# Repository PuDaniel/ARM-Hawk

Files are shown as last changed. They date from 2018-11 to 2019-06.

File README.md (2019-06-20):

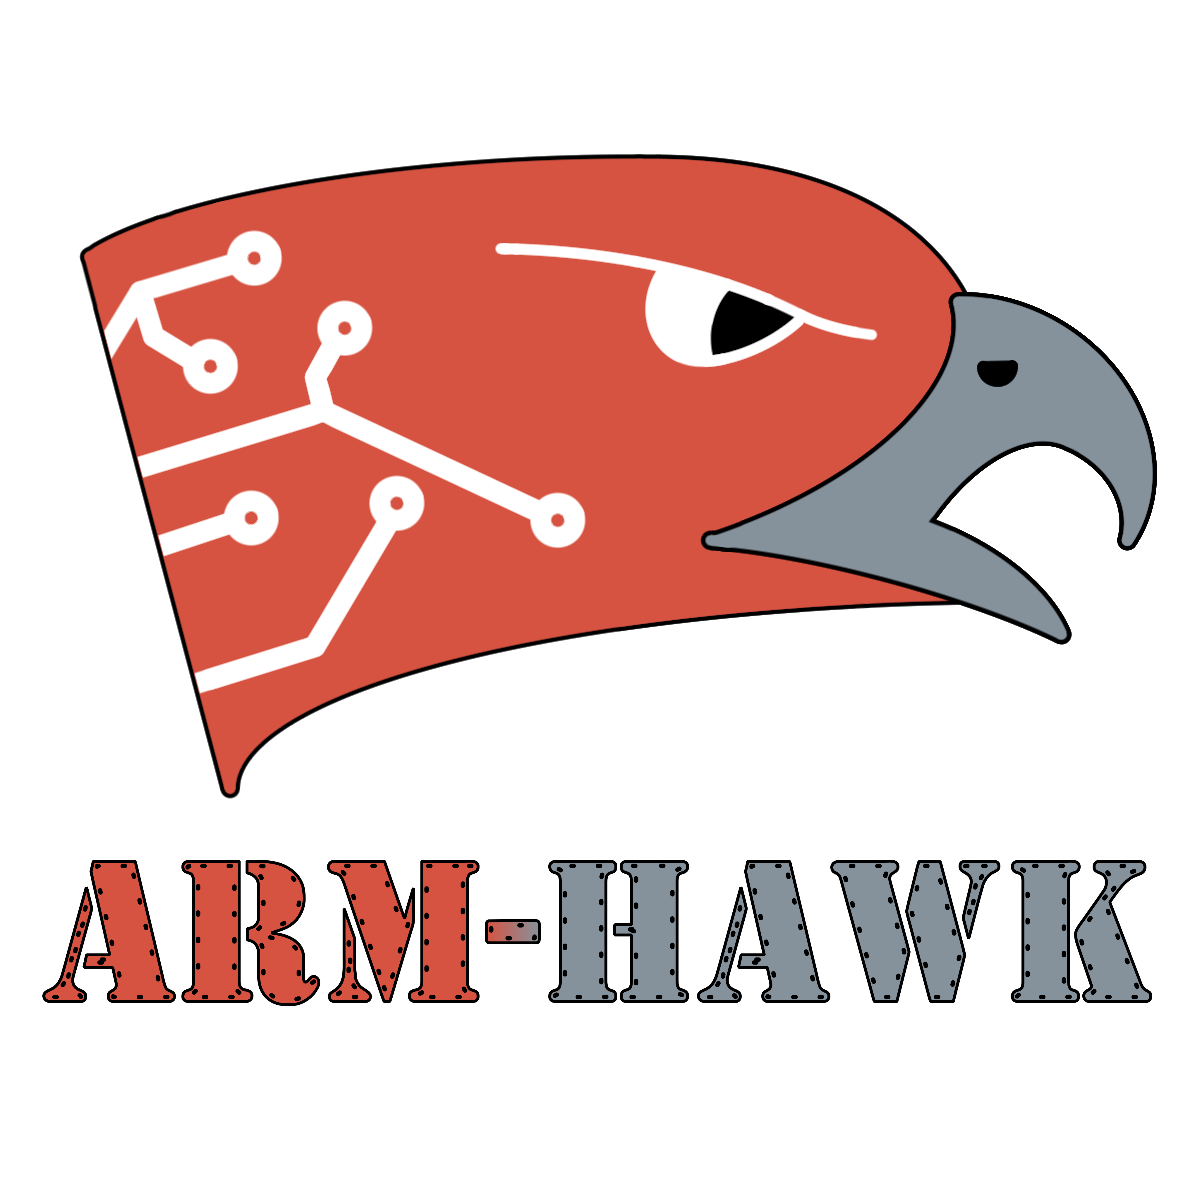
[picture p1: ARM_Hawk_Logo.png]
ARM-Hawk Logo


The ARM-Hawk project consists of a custom designed radio controlled airplane equipped with a scratch built flight computer running custom software. The goal of the project is to develop a system to greatly enhance the flight characteristics of the airplane, as well as to protect its flight envelope.
This repository includes the following parts of the project:

- [ARM_Hawk.pdf](ARM_Hawk.pdf) This file contains a complete description of the project, including the derivation of a flight model and simulation framework, sensor calibration and state estimation algorithms, and the control laws for lateral stability augmentation and stall protection
- [Air_Data_Sensor_Unit](Air_Data_Sensor_Unit) This directory contains information for building and calibrating the custom developed Air Data Probe
- [Airframe](Airframe) This directory contains some information about the airplane used
- [Electronics](Electronics) This directory contains plans for some electronic circuits (RPM sensor, servo switch)
- [Flight_Computer](Flight_Computer) This directory contains the C++ code for the flight software
- [IMU](IMU) This directory contains information for building and calibrating the custom developed Inertial Measurement Unit, as well as a model of the state estimation algorithm

Visit the project's YouTube channel to see some videos of the system in action:
[https://m.youtube.com/channel/UCTHfZXQw1zonnjaXaEWrNzA](https://m.youtube.com/channel/UCTHfZXQw1zonnjaXaEWrNzA)

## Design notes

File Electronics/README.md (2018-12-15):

# Electronics

This directory contains all custom developed circuits used in the ARM-Hawk project.

### Brushless RPM sensor

This sensor is connected to two of the three BLDC motor's phases. It outputs a square wave with a frequency equal to that of the electric field's frequency.

- [Brushless_RPM_sensor/CAM](Brushless_RPM_sensor/CAM) contains g-code files for milling the PCB
- [Brushless_RPM_sensor/KiCad](Brushless_RPM_sensor/KiCad) contains the KiCAD project, as well as the PCB's gerber files

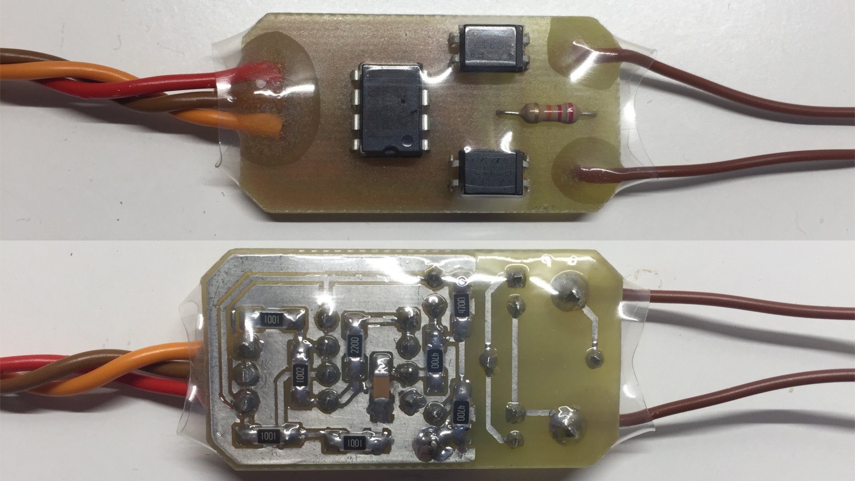
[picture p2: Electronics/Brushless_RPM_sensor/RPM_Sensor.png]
Brushless RPM sensor


### Servoswitch

The servoswitch multiplexes the servo PWM signals coming either form the flight computer or the RC receiver. A PWM channel from the RC receiver can switch all four channel outputs between these two input sources. An ATtiny13 microcontroller executes the task of switching. Many failsafe features are included in the design.

- [Servoswitch/Code](Servoswitch/Code) contains the C program for the microcontroller
- [Servoswitch/KiCad](Servoswitch/KiCad) contains the KiCAD project (only schematic)

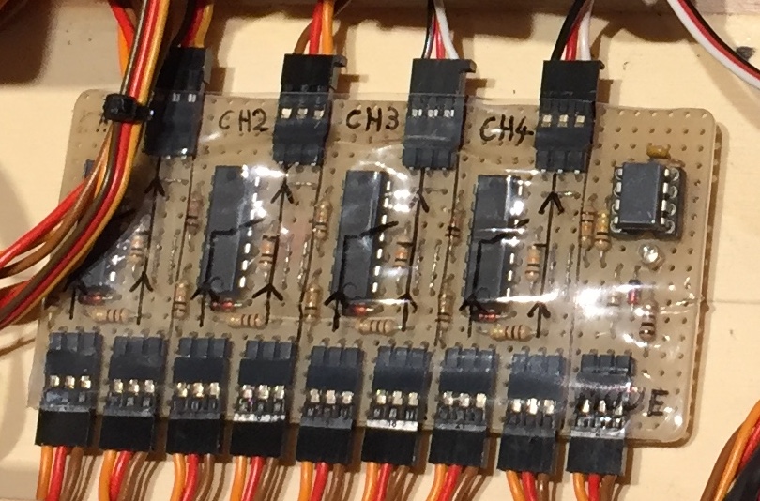
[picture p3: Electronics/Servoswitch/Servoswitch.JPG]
Servoswitch


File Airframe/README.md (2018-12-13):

# Airframe

This directory contains a general plan of the used airplane (custom built) and a *Blender* file of the assembly.

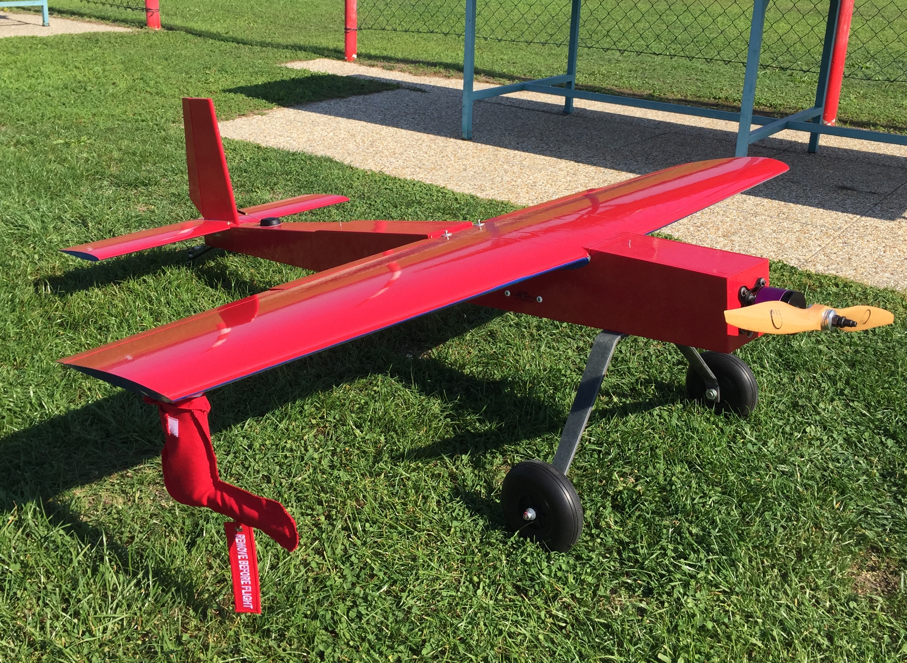
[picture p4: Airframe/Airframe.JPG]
Airframe


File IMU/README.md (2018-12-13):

# IMU

This directory contains all plans to build and calibrate the ARM-Hawk custom designed IMU. It consits of an *NXP FXAS21002* gyroscope and an *NXP FXOS8700* accelerometer/magnetometer. A CNC-machined baseplate provides an exact reference for calibration and mounting in the plane. A 3D-printed case protects the sensor ICs form high-current cables (magnetic fields).

- [Calibration_accelerometer](Calibration_accelerometer) contains a Matlab script to calibrate the accelerometer (a sample dataset and result is also included)
- [Calibration_gyro](Calibration_gyro) contains a Matlab script to calibrate the gyroscope (a sample dataset and result is also included)
- [Calibration_magnetometer](Calibration_magnetometer) contains two Matlab scripts to calibrate the magnetometer for the static case and the dynamic case with the motor running (a sample dataset and result is also included)
- [CAM](CAM) contains the g-code files needed for milling the baseplate (floor), the spacer and the interface PCB, as well as an STL file for 3D-printing the case
- [Jig](Jig) contains a g-code file to mill an alignment jig needed for calibration from an 1.5mm glassfibre plate
- [PCB](PCB) contains the KiCad project of the interface circuit and the PCB's gerber files
- [Simulation](Simulation) contains a *Simulink* model of the state estimation algorithm, which is performed from the flight computer in real time (a sample dataset recorded during a test flight is included)

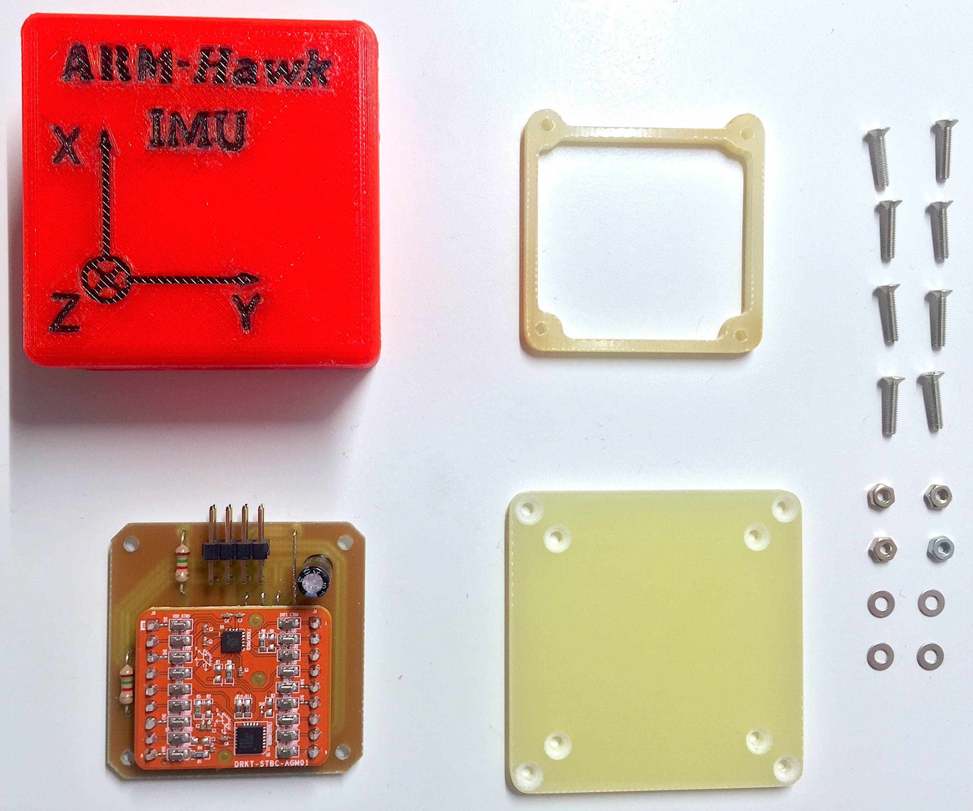
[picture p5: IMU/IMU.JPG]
IMU


CAD drawing with dimensions and rendering of the case:

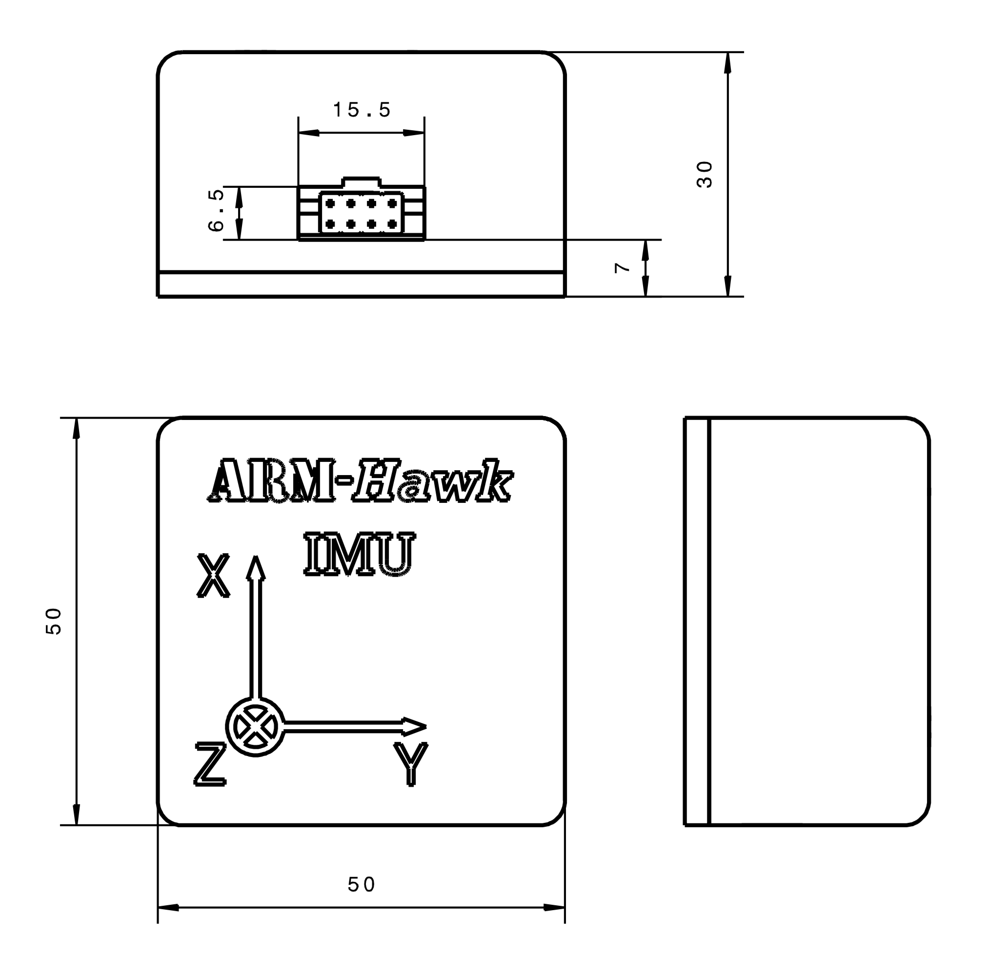
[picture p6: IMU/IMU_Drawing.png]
IMU Drawing


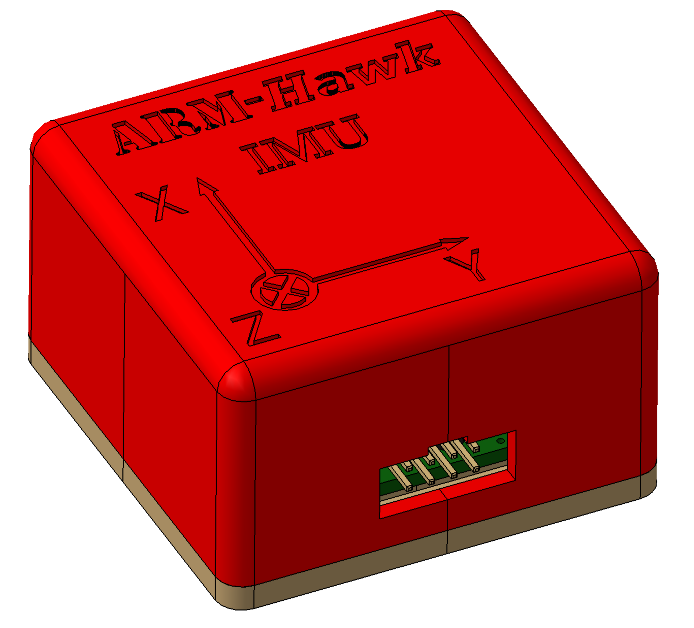
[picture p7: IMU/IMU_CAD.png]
IMU CAD


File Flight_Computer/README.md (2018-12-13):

# Flight Computer

This directory contains the flight computer's C++ software. The project has been created with *System Workbench for STM32 by AC6* ([http://www.openstm32.org](http://www.openstm32.org)).

The used hardware is an STM32F767ZI on a Nucleo development board (from ST), powered from a simple power supply providing 5V and 3.3V. Additionally, a *Sparkfun Venus638 GPS breakout* is used. All this is located in the rear equipment bay of the plane:

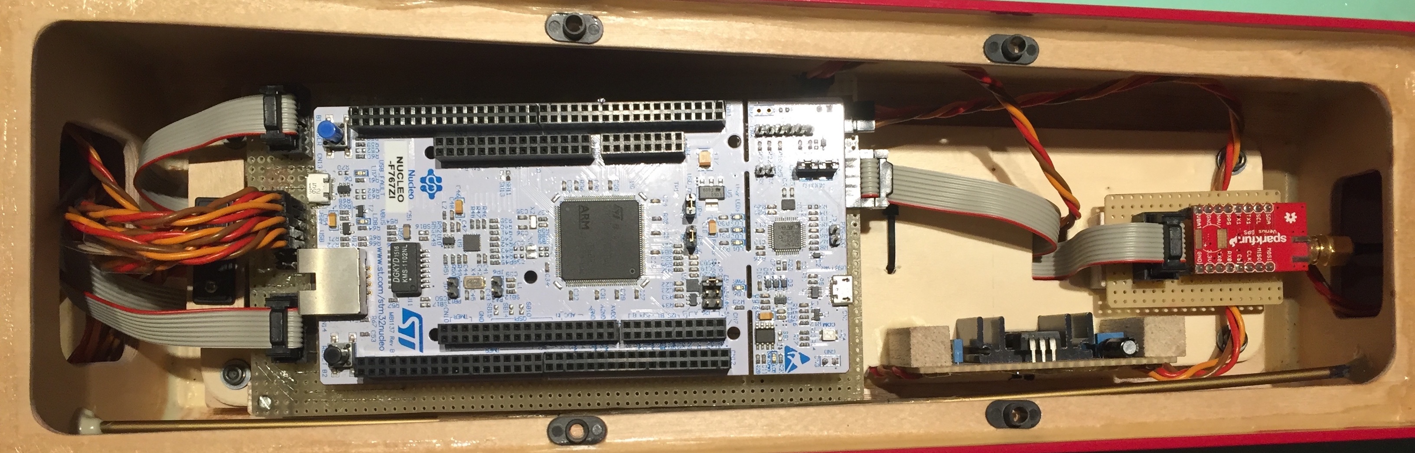
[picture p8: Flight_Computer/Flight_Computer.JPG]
Flight Computer


The Nucleo board is connected to all sensors and the datalog via a prototype interface PCB:

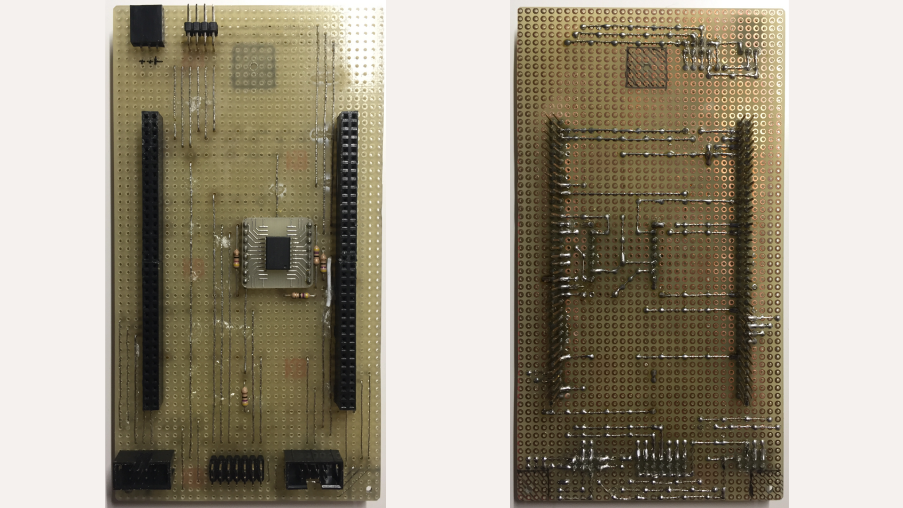
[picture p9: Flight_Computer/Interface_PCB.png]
Interface PCB


The forward (underwing) equpiment area holds the RC equipment, as well as the [Servoswitch](/Electronics/Servoswitch) and the [IMU](/IMU):

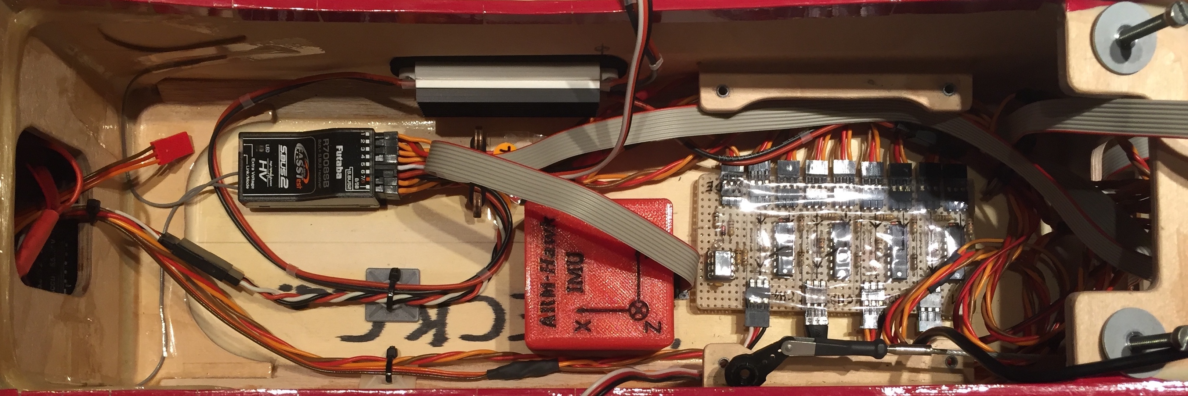
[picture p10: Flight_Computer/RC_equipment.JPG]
RC equipment


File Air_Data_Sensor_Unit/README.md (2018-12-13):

# Air Data Sensor Unit

This directory contains all plans to build the mechanical and electronical assembly of the Air Data Sensor Unit, as well as supporting files for obtaining calibrated measurements.

- [CAM](CAM) contains the g-code files for milling the two aluminum pieces (base and tip), the glassfibre mount, and the PCB, as well as STL files for the housing (3D-printed with PLA)
- [CFD](CFD) contains the pressure coefficient at the probe's tip computed with *ANSYS*, as well as the calibration curve for the static pressure port
- [Matlab](Matlab) contains three scripts for calculating the realtions between differential pressures and the flow parameters (airspeed, alpha, beta), as well as a set of precomputed characteristics:
  - *alpha_beta_algorithm.m* Computes alpha, beta and airspeed from the three measured differential pressures iteratively
  - *characterisitic.m* Computes and plots characteristic curves of alpha and beta for fixed total pressures
  - *lookup_table.m* Computes a lookup table to be used in real time from the flight computer (result of script is found in [AirDataComputer_data.cpp](/Flight_Computer/Main/sensors/AirDataComputer_data.cpp))
- [PCB](PCB) contains the KiCad project of the sensor circuit, along with the gerber files of the PCB

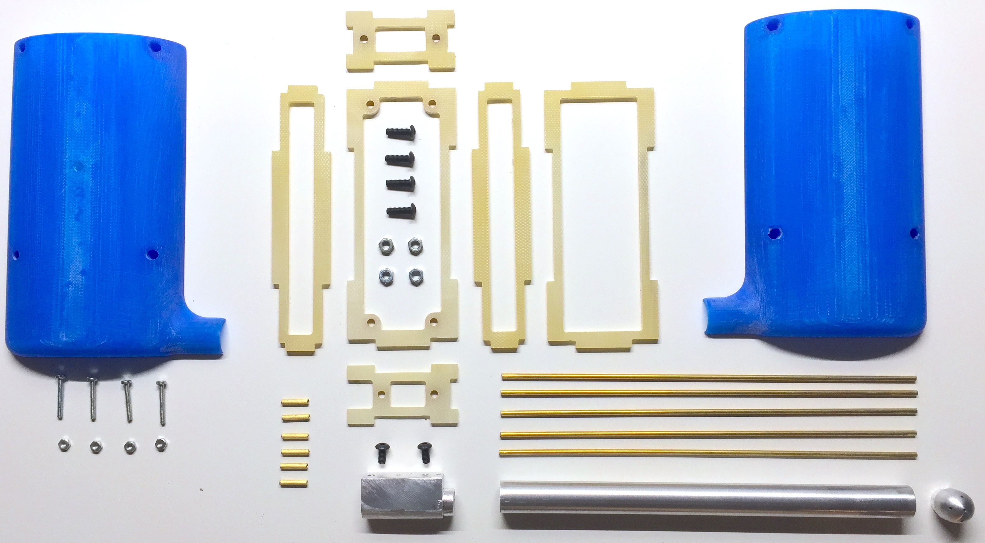
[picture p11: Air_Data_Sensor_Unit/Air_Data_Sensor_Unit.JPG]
Air Data Sensor Unit


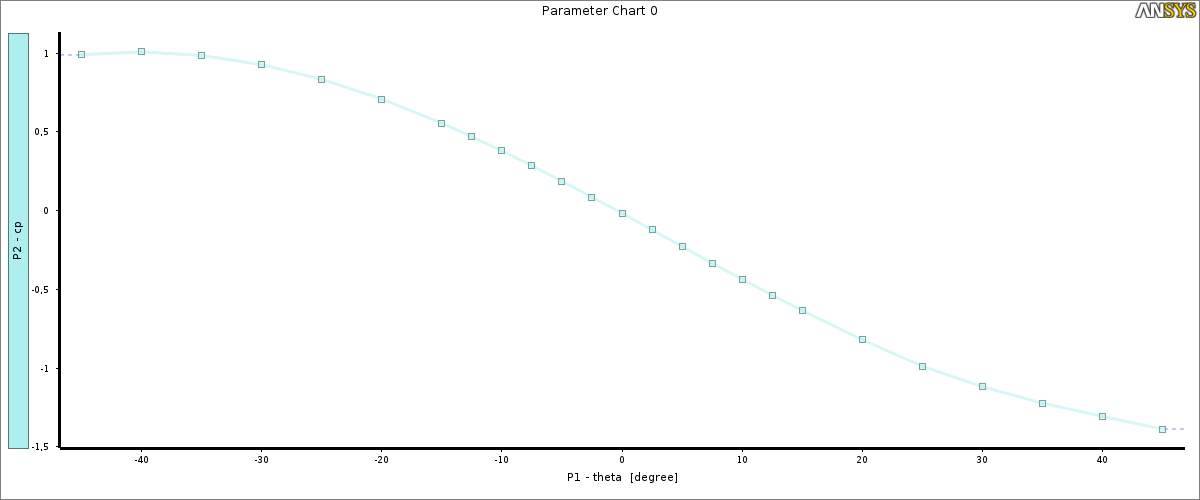
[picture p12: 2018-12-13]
Air_Data_Sensor_Unit/CFD/cp_over_theta.png

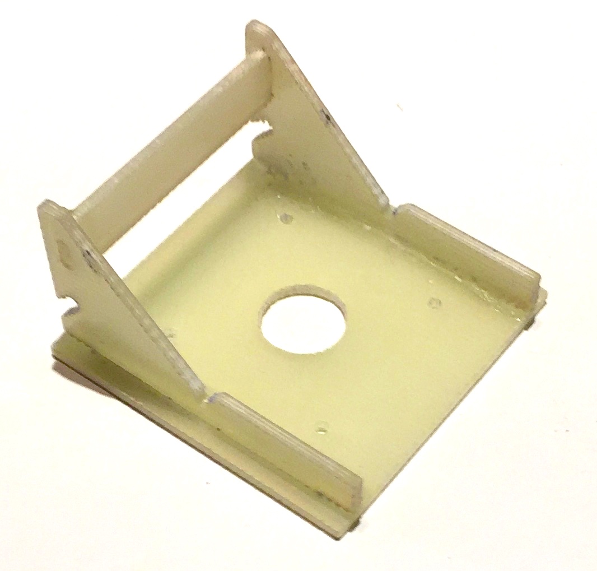
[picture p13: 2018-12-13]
IMU/Jig/Jig.JPG

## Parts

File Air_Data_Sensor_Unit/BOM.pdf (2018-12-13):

### Air Data Sensor Unit PCB Components

Quantity | Name | Package
1 | 2x4 Pin Header 2.54mm Pitch | SMD
5 | Resistor 10k | 1206
3 | Resistor 1k | 1206
3 | Capacitor 100n | 1206
3 | NPN Transistor MMBT2222 | SOT-23
1 | SMI Pressure SensorSM9541-020C-D-C-3-S | SOIC-16W
2 | SMI Pressure Sensor SM9541-010C-D-C-3-S | SOIC-16W
1 | Sparkfun SEN-09694 BMP085 Pressure Sensor | Breakout Board

### Air Data Sensor Unit Parts

Quantity | Name | Material
1 | Sensor PCB | -
1 | Probe tip | Aluminum
1 | Probe base | Aluminum
1 | Probe tube ø10x1x150 | Aluminium
5 | Pressure tube ø0.5x0.25x150 | Brass
6 | Pressure fitting (use short sections of ø0.5x0.25 tube) | Brass
1 | Robart airline tubing (1/8’’ OD, 1/16’’ ID) | Tubing
6 | CNC cut mount pieces | Glassfibre plate 3mm
1 | 3D printed housing (left and right) | PLA
4 | Socket head cap screw M3x10 | Steel
2 | Socket head cap screw M3x6 | Steel
6 | M3 hex nut | Steel
4 | Socket head cap screw M2x12 | Steel
4 | M2 hex nut | Steel

1

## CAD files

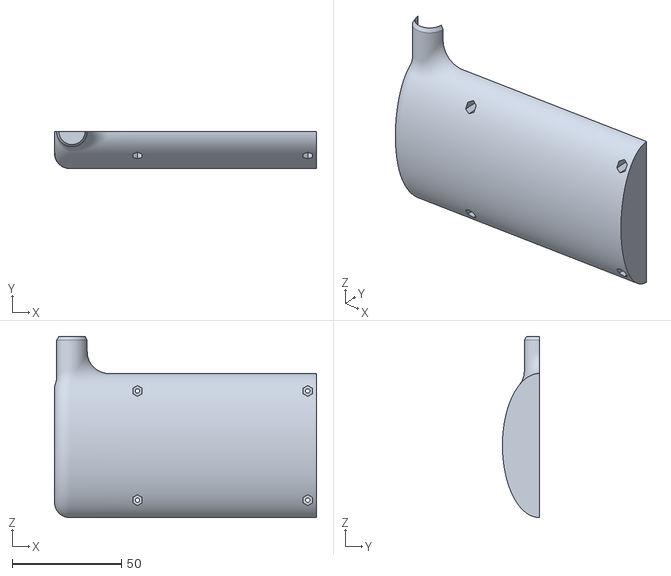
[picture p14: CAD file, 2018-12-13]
Air_Data_Sensor_Unit/CAM/Housing/housing_left.stl
120.0 x 17.0 x 83.0

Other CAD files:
Air_Data_Sensor_Unit/CAM/Housing/housing_right.stl

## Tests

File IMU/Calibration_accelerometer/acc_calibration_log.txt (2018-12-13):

 
Calibration form: f = C*(f_acc - f_0)
 
Local magnitude of gravity vector [m/s^2]=
   9.8082e+00

Calibration matrix C=
   9.8459e-01   8.0660e-04  -2.3062e-02
  -3.3592e-03   1.0027e+00   2.4024e-03
   4.9667e-03  -3.3054e-03   1.0109e+00

Acceleration bias vector f_0 [m/s^2]=
  -7.6722e-02
  -8.5341e-02
  -7.2458e-02

Error before calibration [%]=
   2.0403e+00

Error after calibration [%]=
   5.8813e-01

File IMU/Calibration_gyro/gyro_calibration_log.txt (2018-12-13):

 
Calibration form: omega_v = C*(omega_gyro - omega_0) - G*f
 
Calibration matrix C=
   1.0313e+00  -1.1339e-02  -7.2564e-03
  -7.8347e-03   9.8760e-01   7.4846e-03
   1.9856e-03   6.5120e-04   1.0242e+00

Angular rate bias vector omega_0 [rad/s]=
   6.9040e-02
  -4.8245e-02
   4.1435e-03

G-force coupling matrix G [rad*s/m]=
   1.0539e-03            0            0
            0   9.4485e-04            0
            0            0   1.2274e-03

Error before calibration [%]=
   3.2692e+00

Error after calibration [%]=
   1.0893e+00

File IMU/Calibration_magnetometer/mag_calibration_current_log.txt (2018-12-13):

 
Calibration form: B_M = S * M * B_E + B_0 + I*B_I
                  B_E = C * (B_M - B_0 - I*B_I)
 
Current dependent hard-iron offset vector B_I [T/A]=
   8.2807e-09
   1.2813e-08
  -2.3106e-08

Error before calibration [%]=
   4.0295e-01

Error before calibration [%]=
   1.6261e-01

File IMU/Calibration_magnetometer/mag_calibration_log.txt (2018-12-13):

 
Calibration form: B_M = S * M * B_E + B_0
                  B_E = (S * M)^(-1) * (B_M - B_0)
                  B_E = C * (B_M - B_0)
 
Local magnetic field vector [T]=
   2.1048e-05
   1.5839e-06
   4.3789e-05

Scale matrix S=
   9.5256e-01   2.7014e-04   1.0733e-02
   2.7014e-04   9.2349e-01   2.4467e-03
   1.0733e-02   2.4467e-03   9.3279e-01

Misalignment matrix M=
   9.9948e-01  -1.6256e-02  -2.7758e-02
   1.6420e-02   9.9985e-01   5.7045e-03
   2.7661e-02  -6.1573e-03   9.9960e-01

Calibration matrix C=
   1.0491e+00   1.7427e-02   1.7537e-02
  -1.7268e-02   1.0827e+00  -9.2422e-03
  -4.1222e-02   3.3487e-03   1.0721e+00

Hard-iron offset vector B_0 [T]=
  -1.0318e-04
  -6.9476e-05
  -7.3740e-05

Error before calibration [%]=
   4.5485e-01

Error before calibration [%]=
   2.5320e-01

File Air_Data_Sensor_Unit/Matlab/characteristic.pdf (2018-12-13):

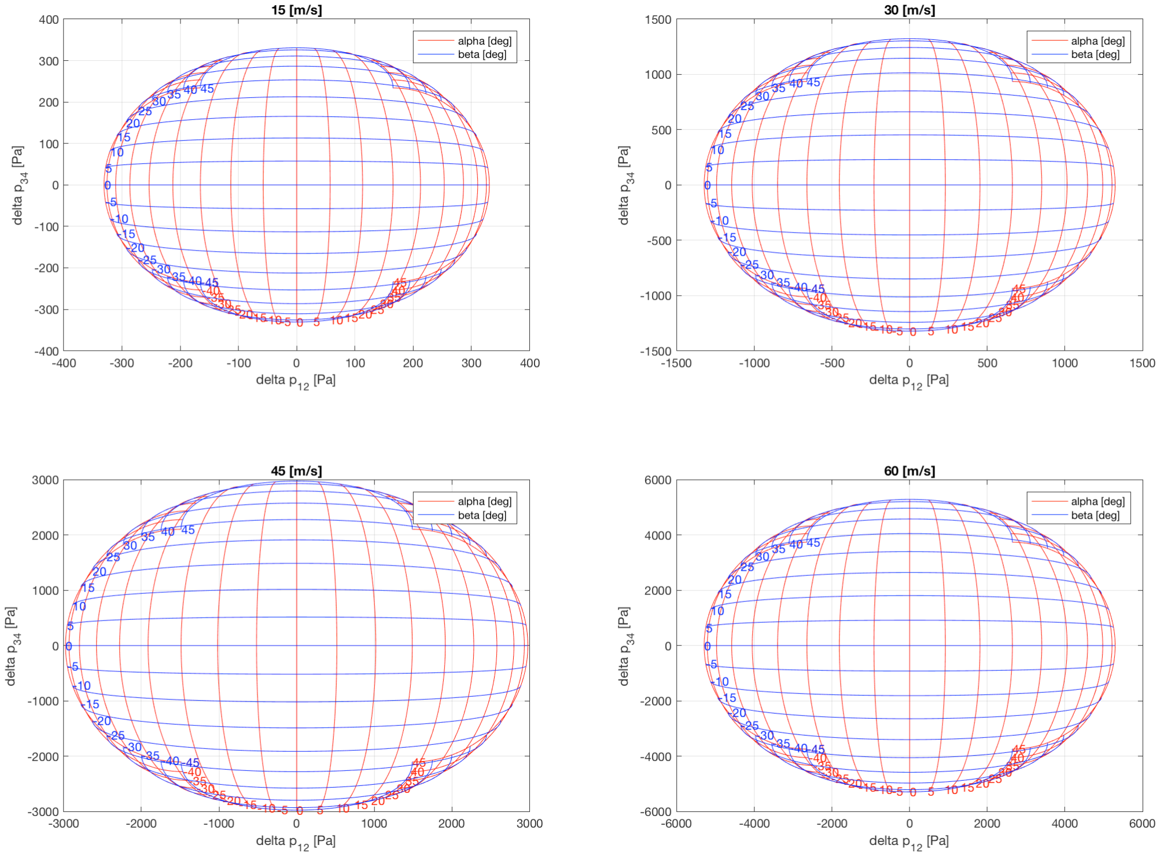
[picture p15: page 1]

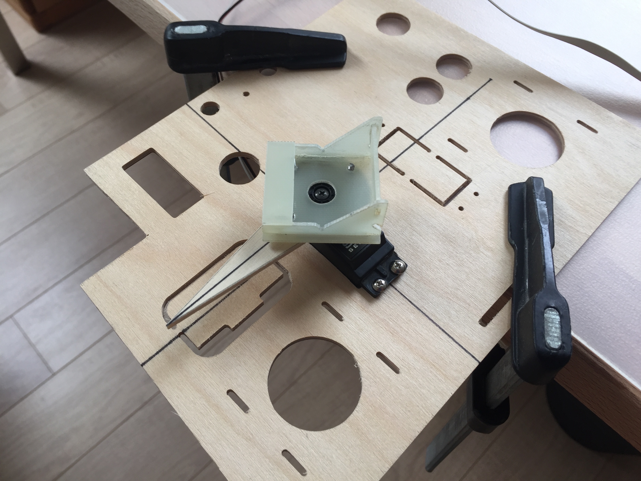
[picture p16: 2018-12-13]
IMU/Calibration_gyro/gyro_calibration_1.JPG

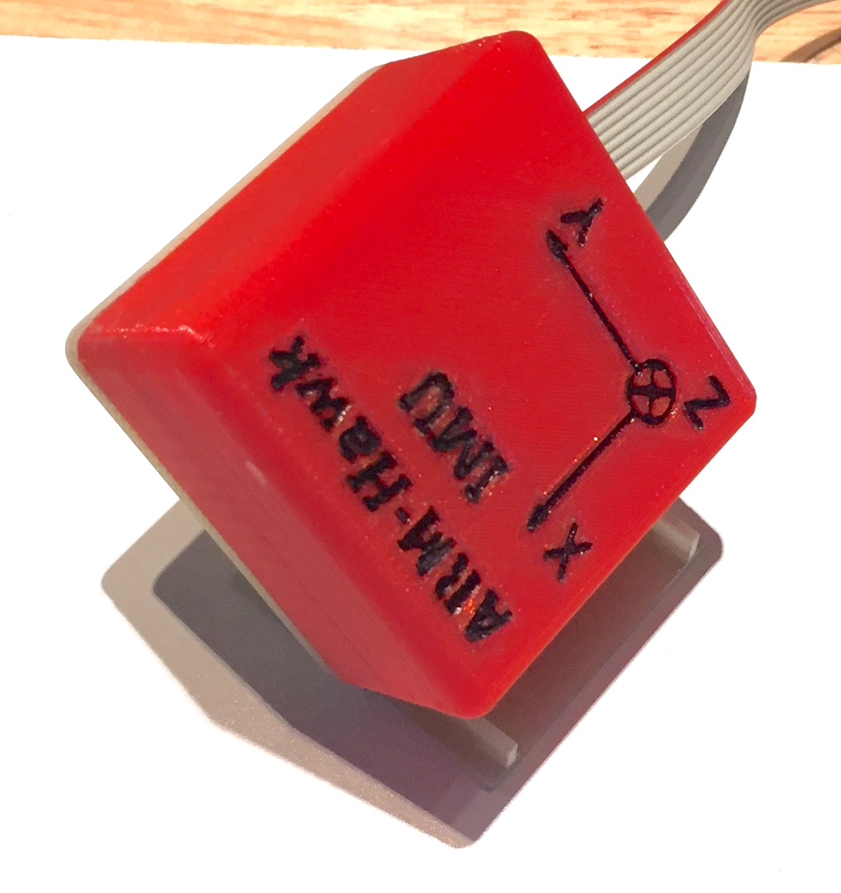
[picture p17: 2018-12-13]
IMU/Calibration_accelerometer/acc_calibration.JPG

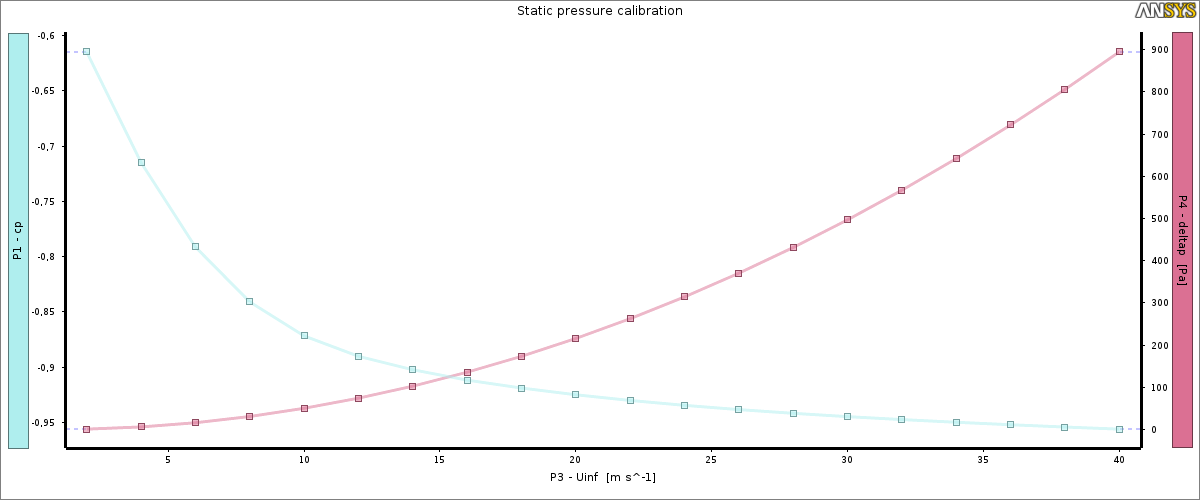
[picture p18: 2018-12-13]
Air_Data_Sensor_Unit/CFD/static_port_calibration.png

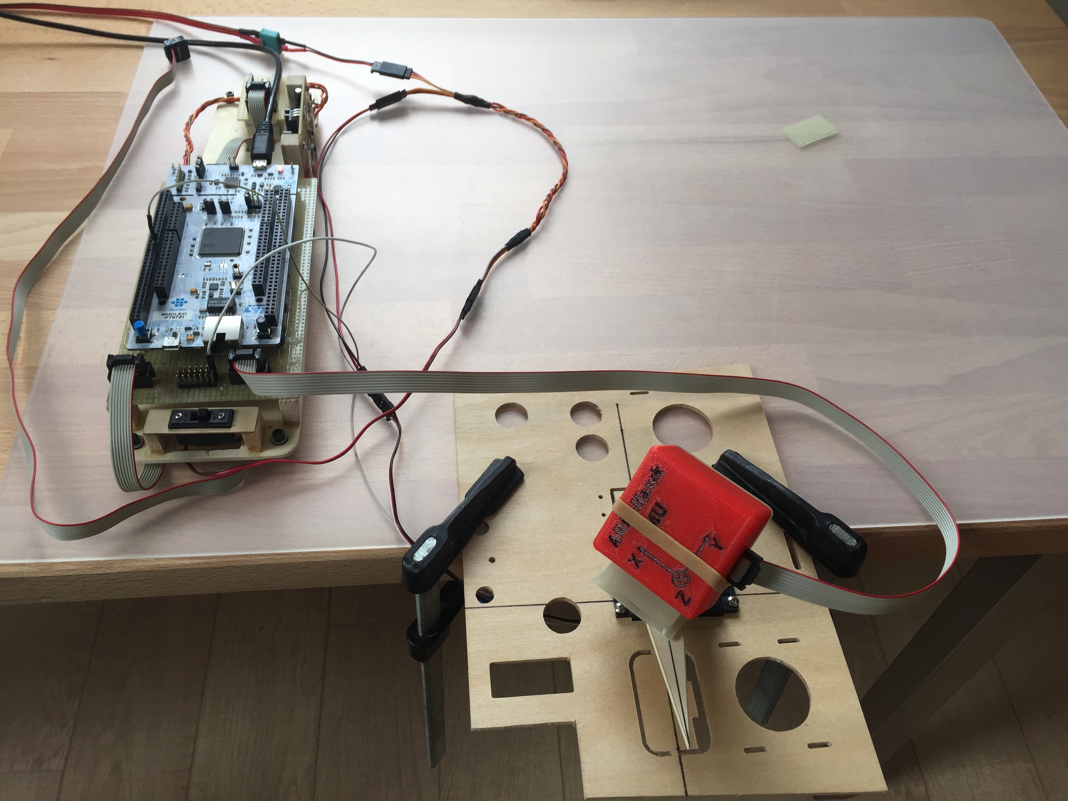
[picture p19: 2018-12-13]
IMU/Calibration_gyro/gyro_calibration_2.JPG

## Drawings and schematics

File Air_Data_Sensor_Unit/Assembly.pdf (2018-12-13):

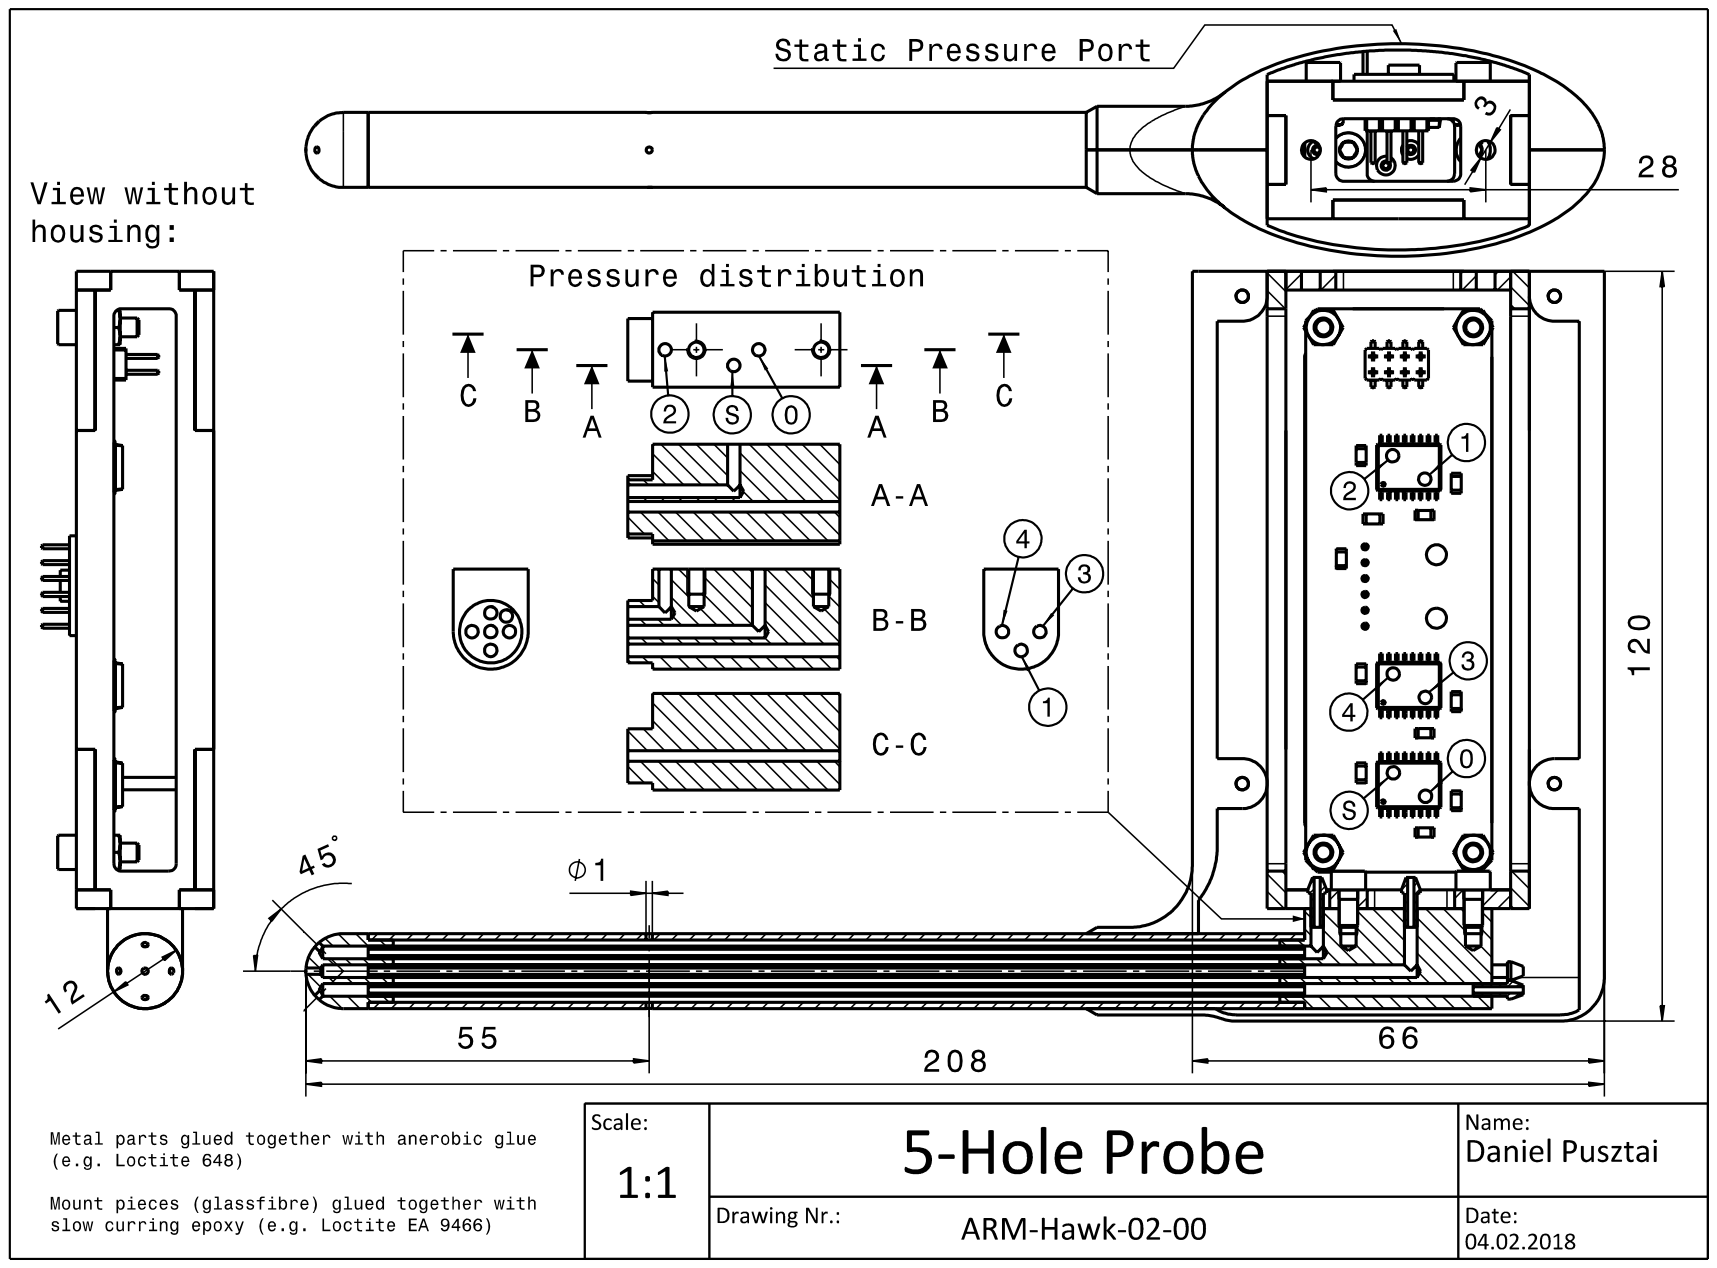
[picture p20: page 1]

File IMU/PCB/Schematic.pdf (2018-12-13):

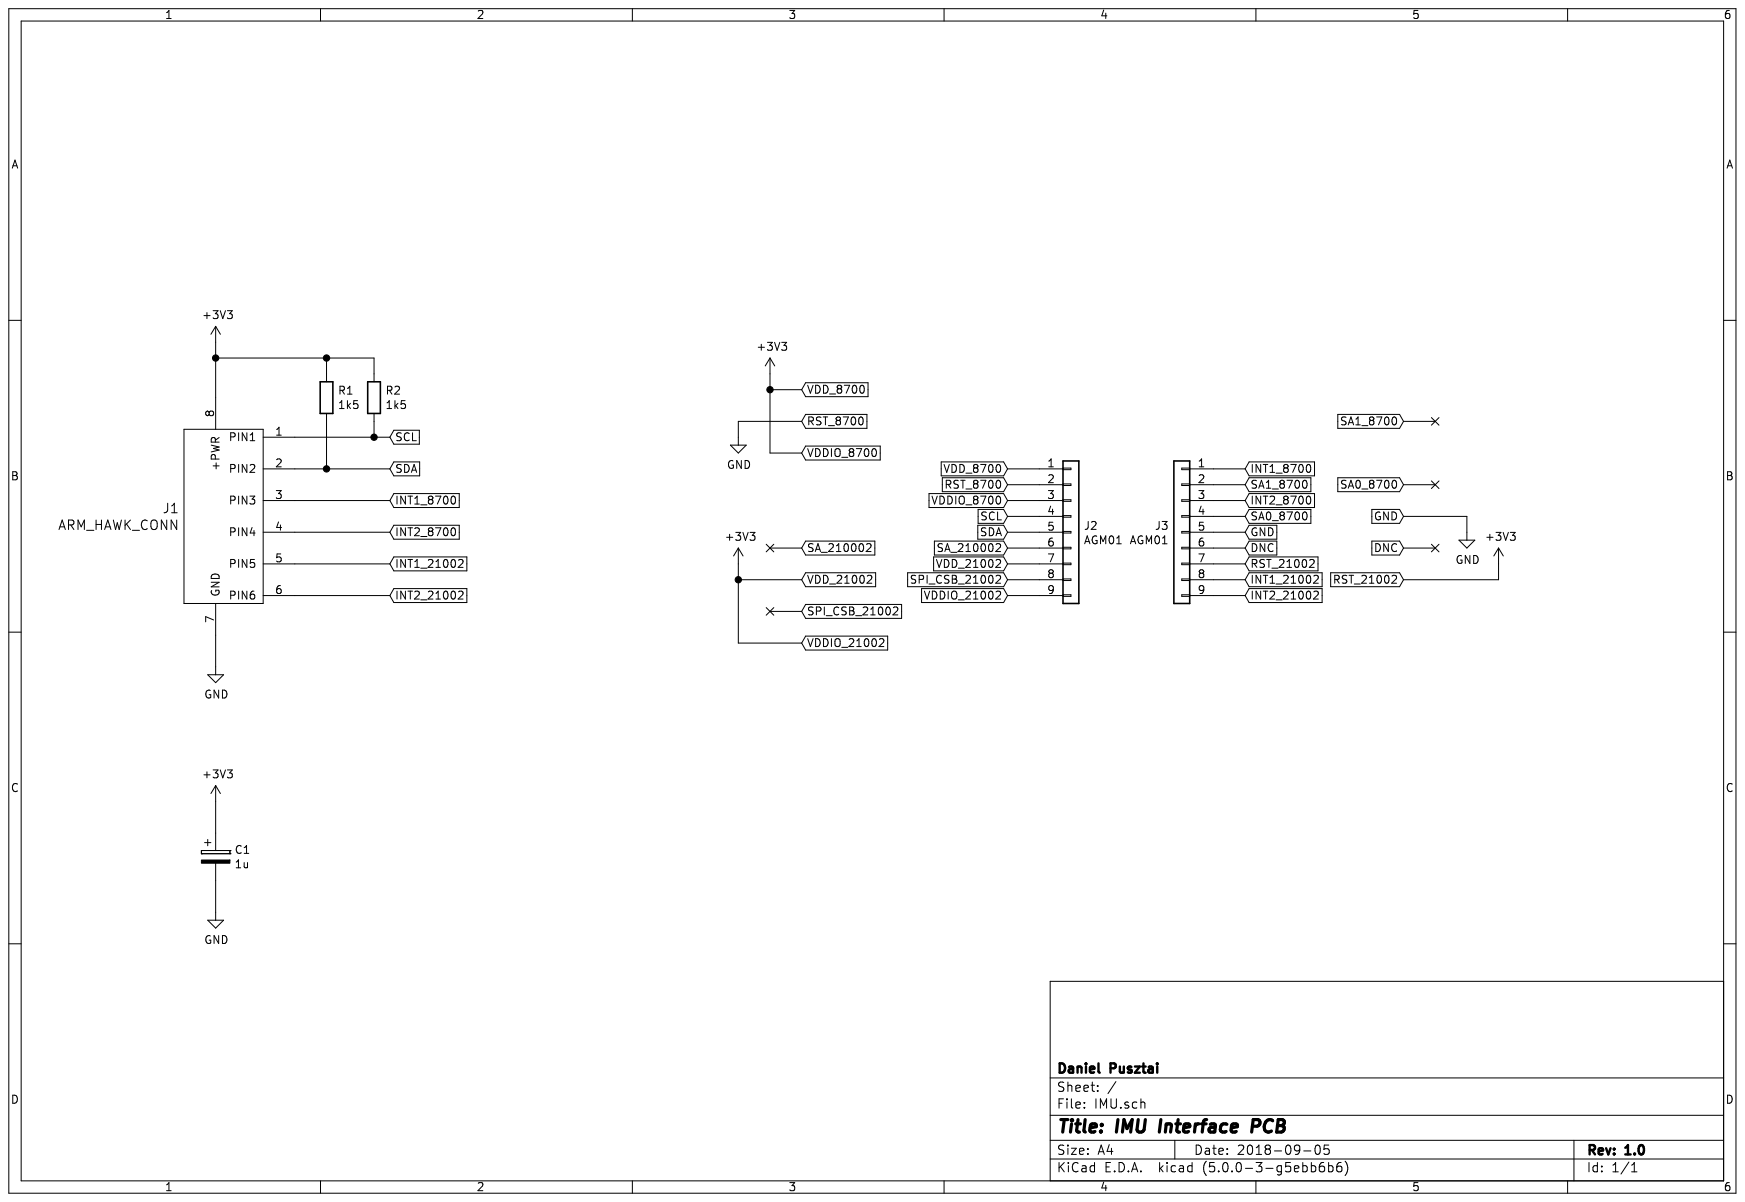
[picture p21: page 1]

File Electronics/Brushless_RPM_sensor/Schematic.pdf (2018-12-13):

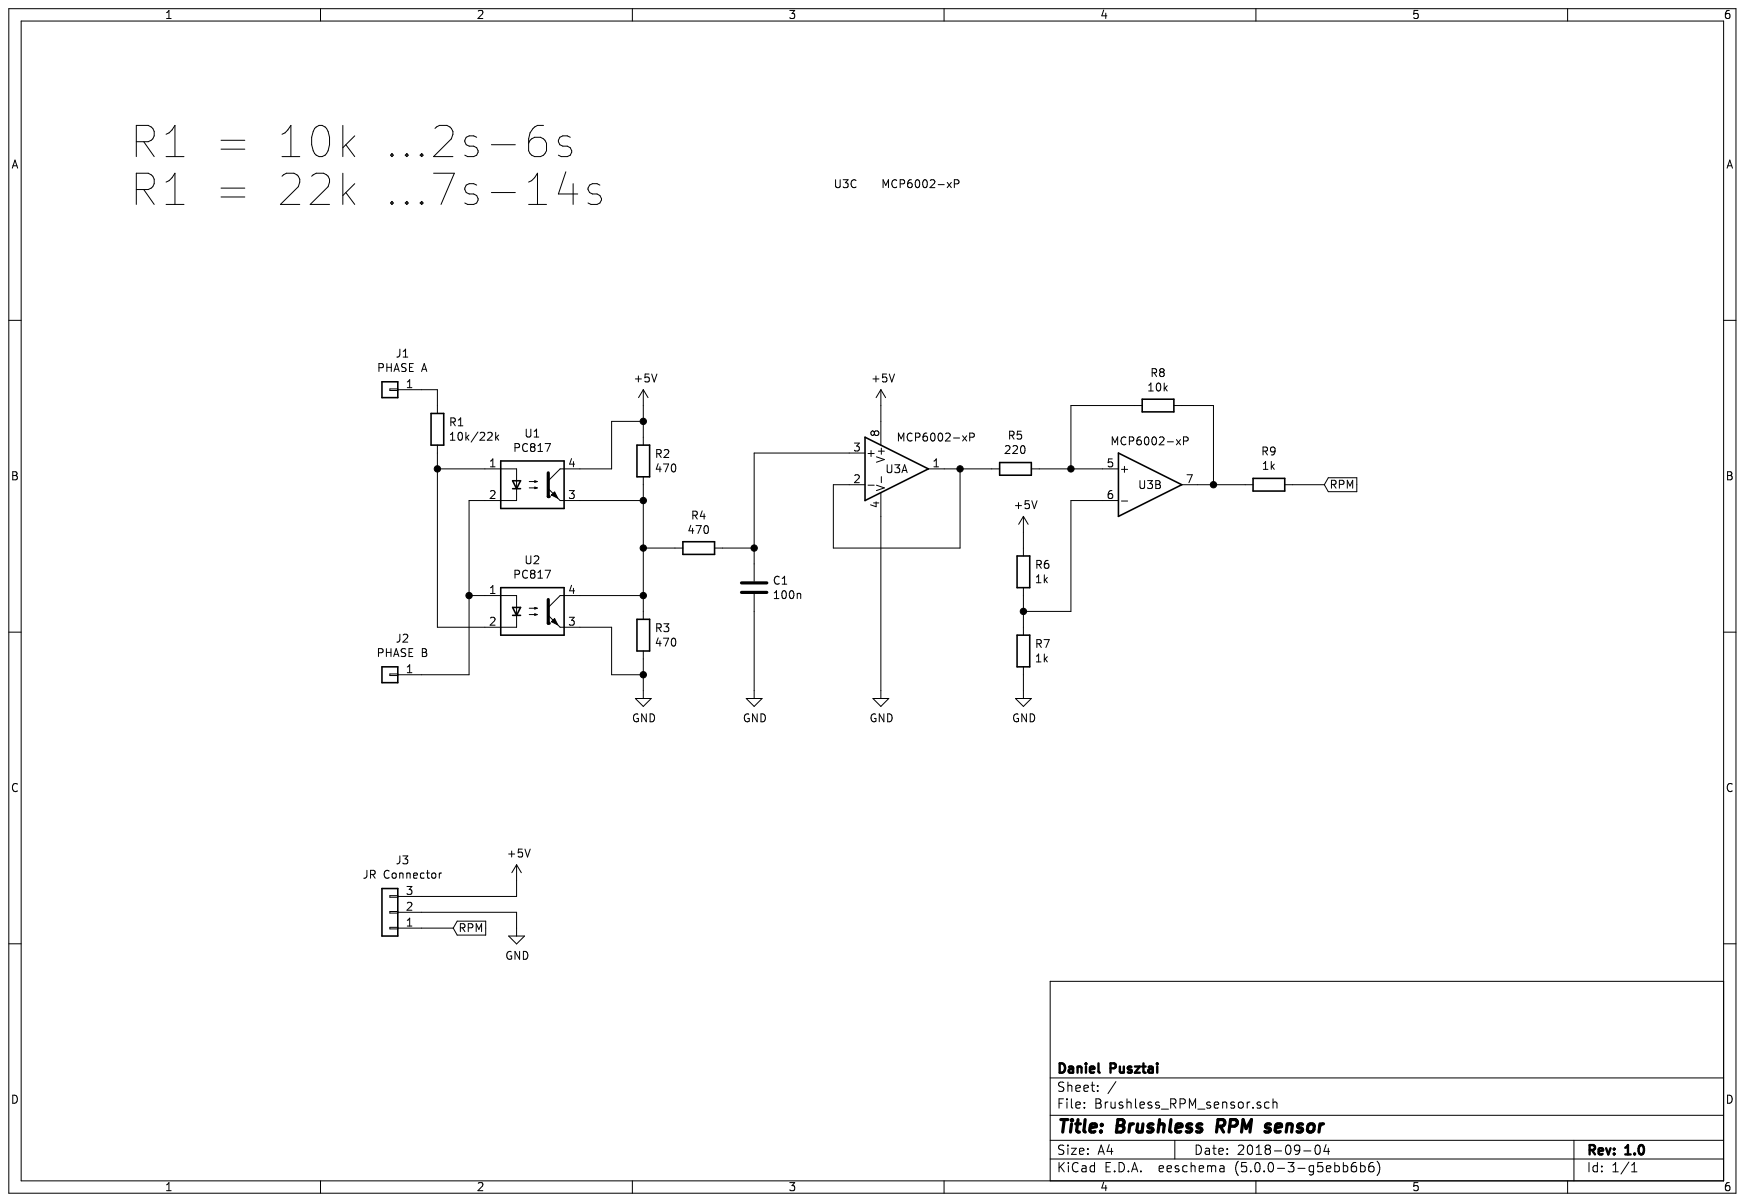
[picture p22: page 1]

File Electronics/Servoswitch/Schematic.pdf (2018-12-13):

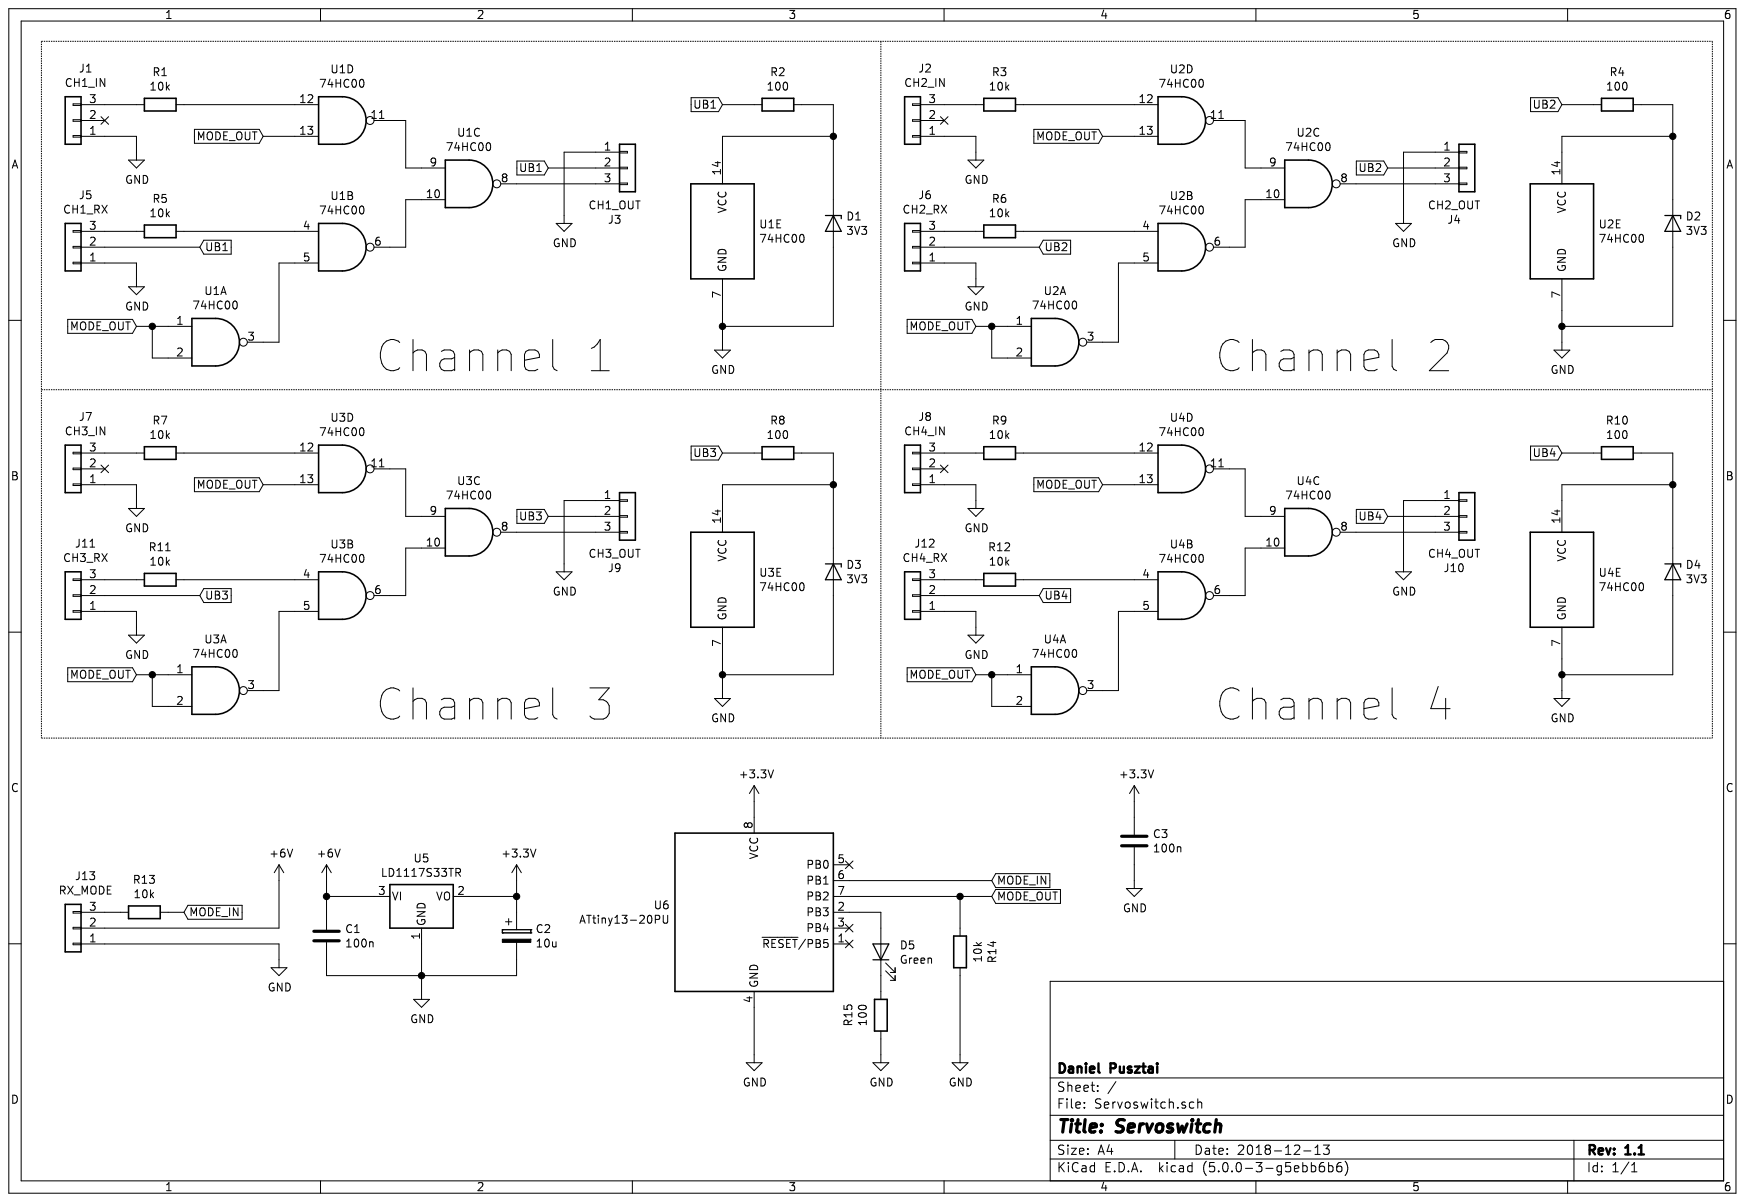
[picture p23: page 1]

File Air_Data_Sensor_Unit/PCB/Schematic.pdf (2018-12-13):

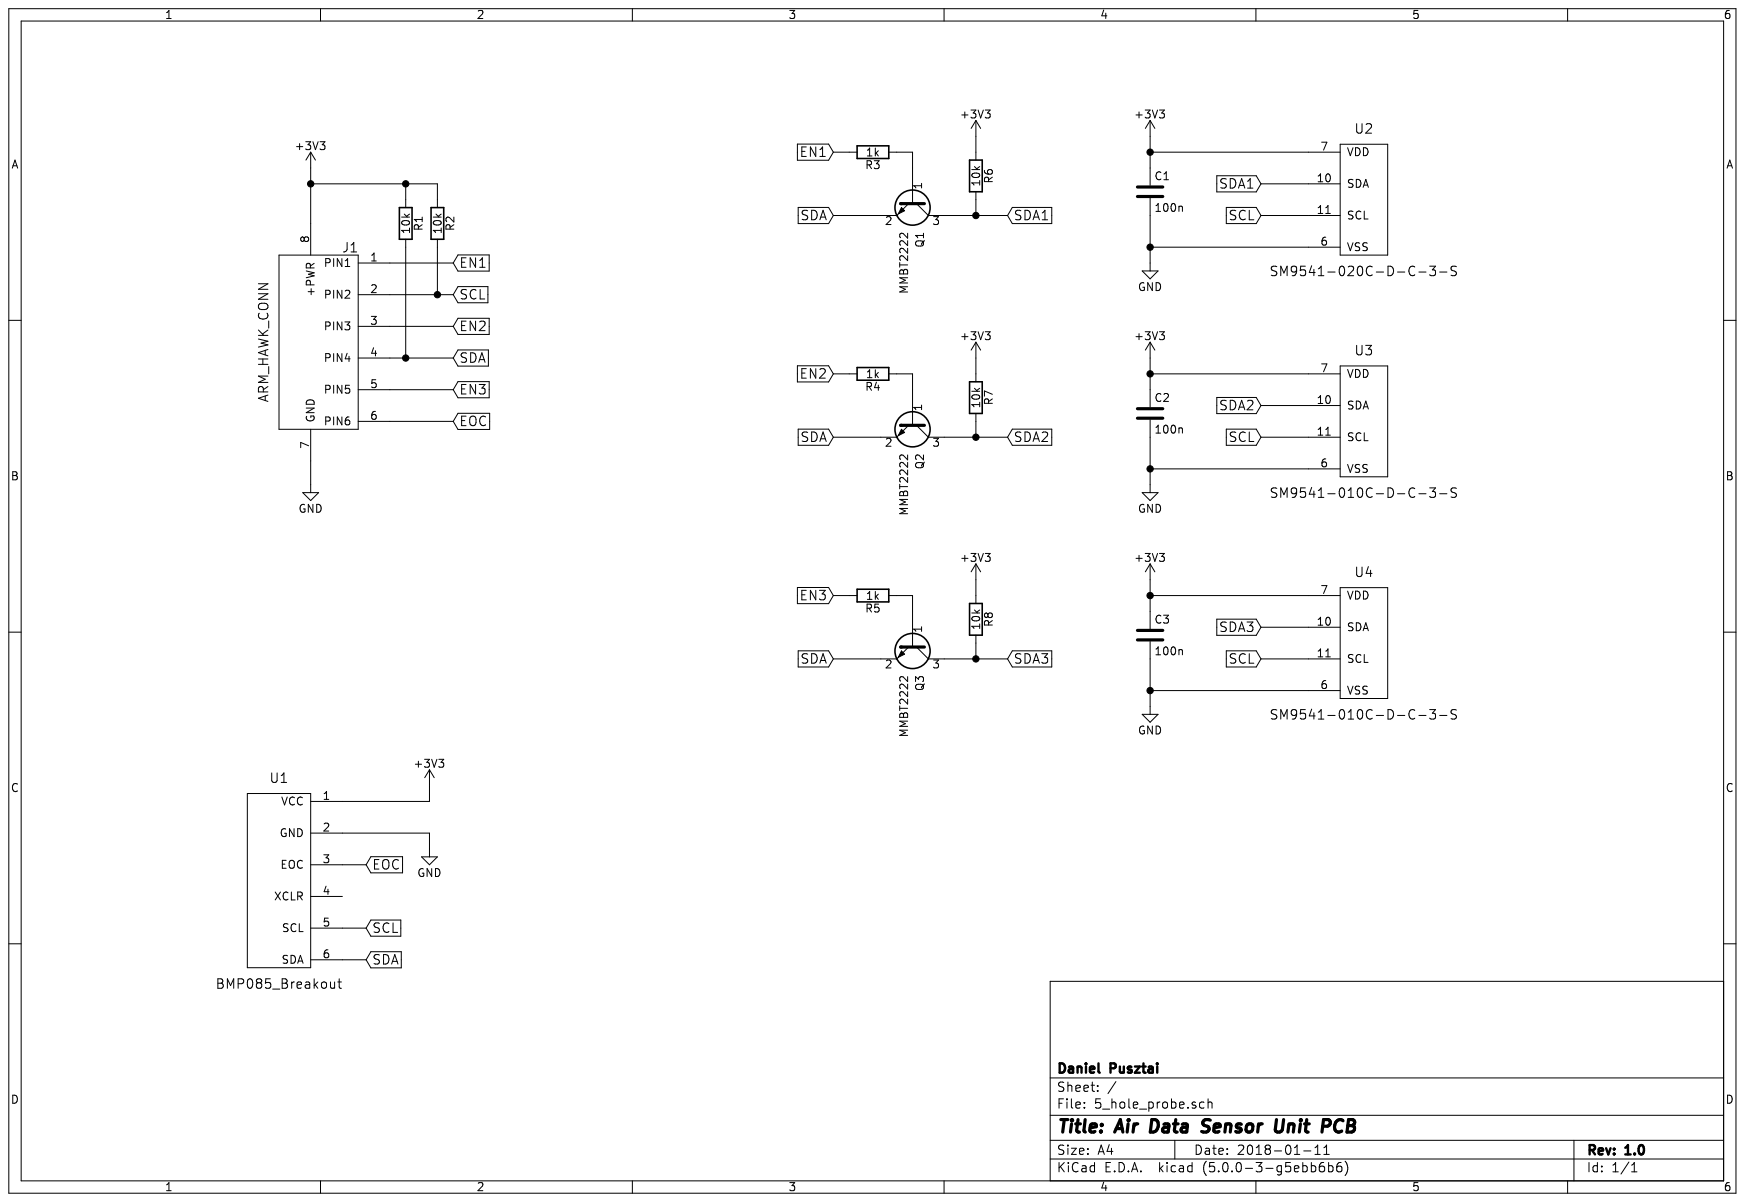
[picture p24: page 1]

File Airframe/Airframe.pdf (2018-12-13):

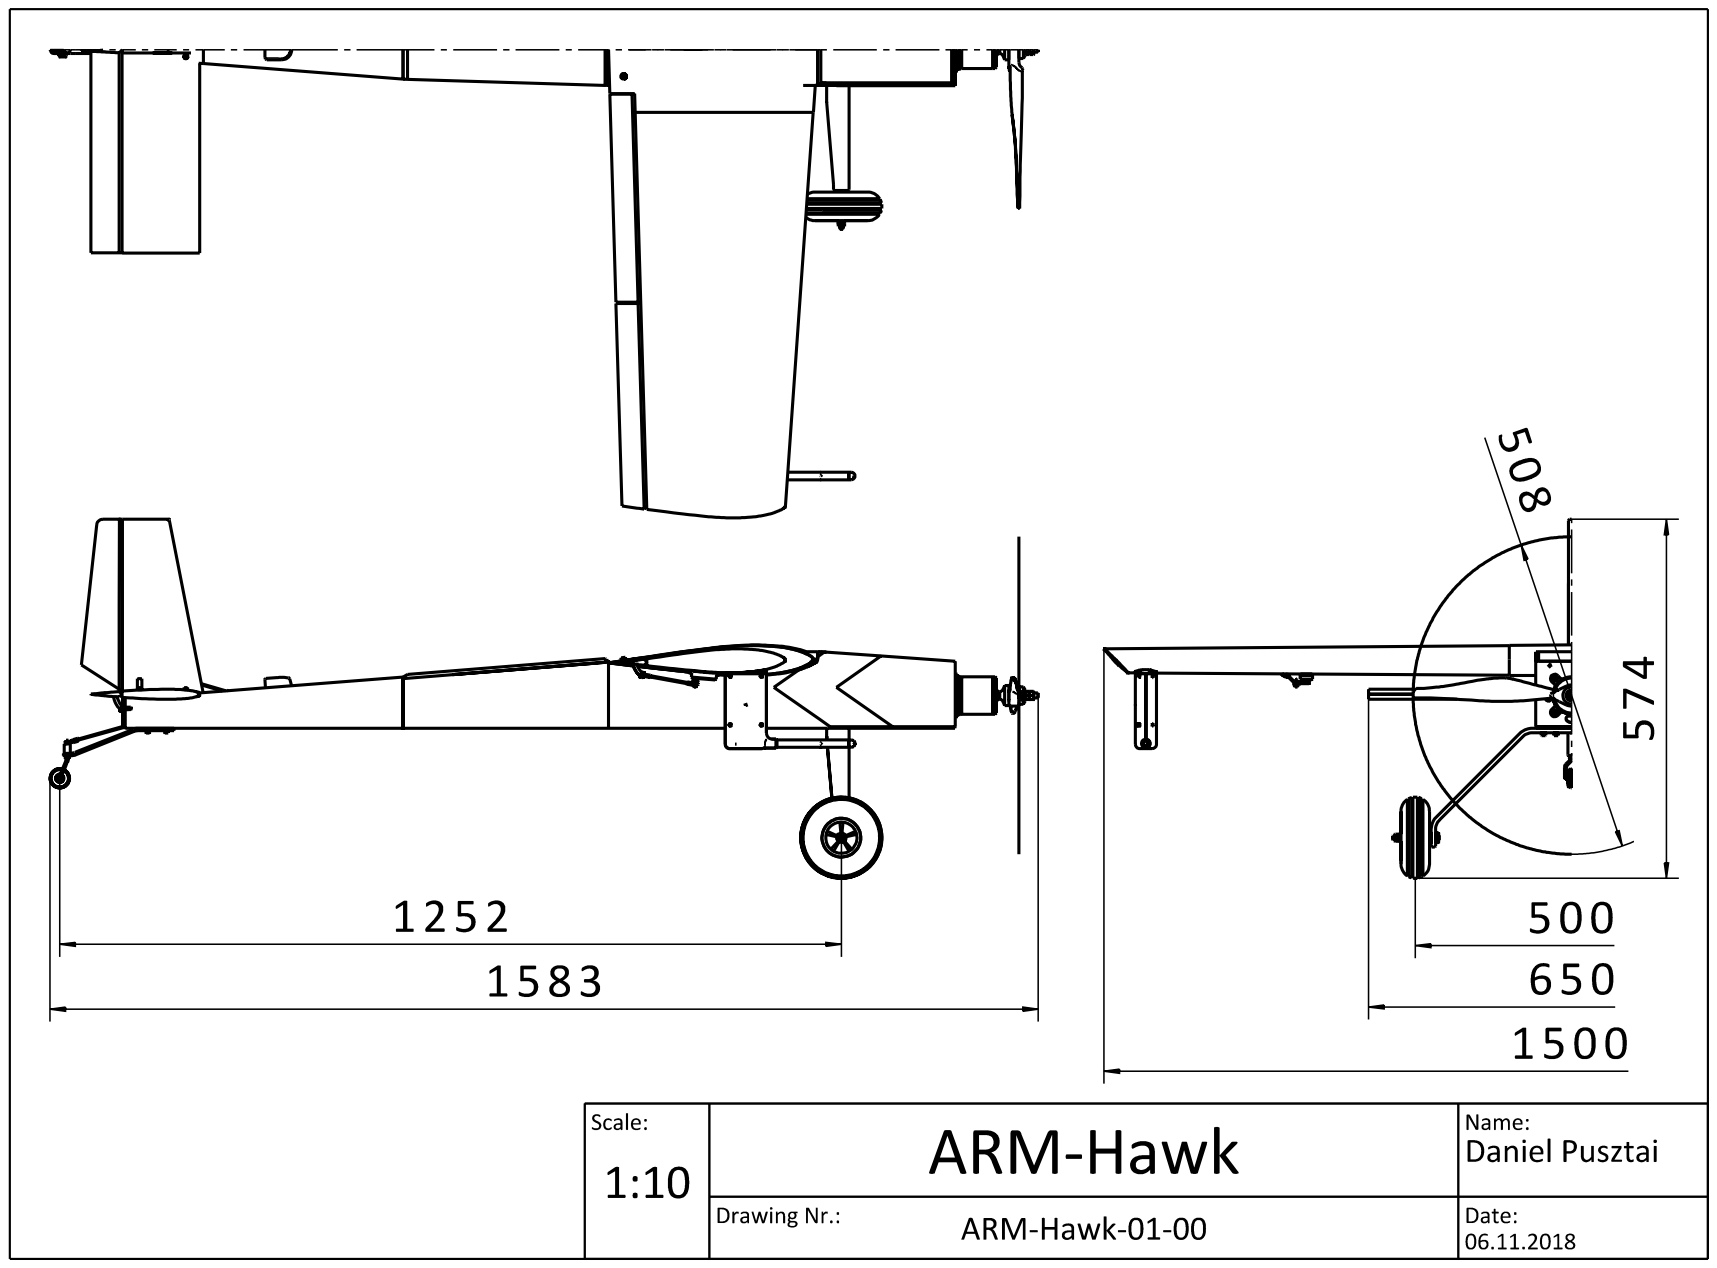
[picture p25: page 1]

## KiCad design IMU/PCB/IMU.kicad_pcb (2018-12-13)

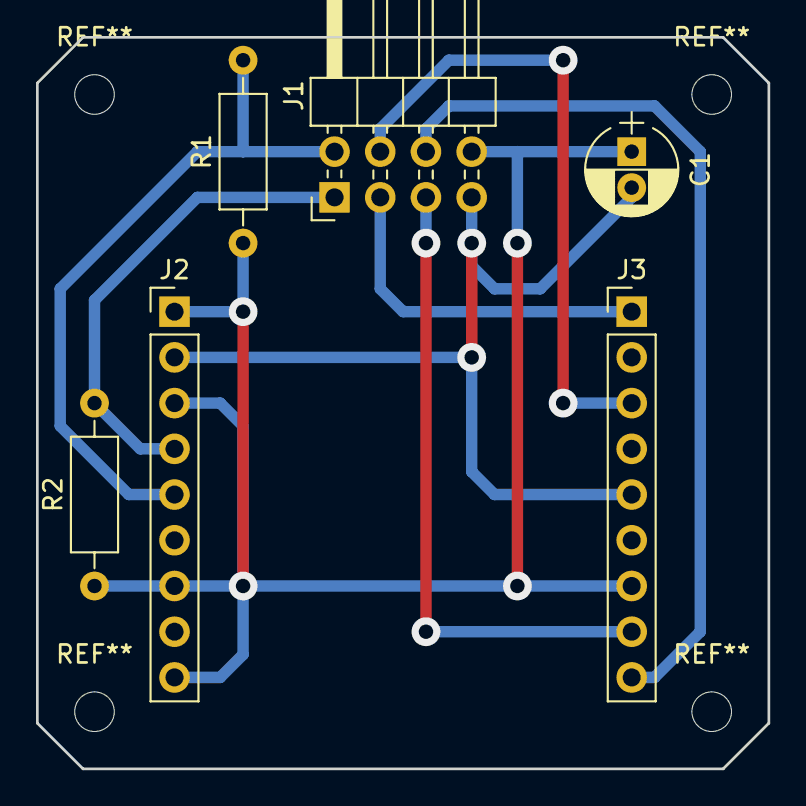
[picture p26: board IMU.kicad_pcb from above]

Board: 2 copper layers, 40.6 x 40.6 mm, 6 parts (0 on the bottom side), 8 nets.

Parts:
C1: 1u; CP_Radial_D5.0mm_P2.00mm
J1: ARM_HAWK_CONN; Pin_Header_Angled_2x04_Pitch2.54mm
J2, J3: AGM01; Pin_Header_Straight_1x09_Pitch2.54mm
R1, R2: 1k5; R_Axial_DIN0207_L6.3mm_D2.5mm_P10.16mm_Horizontal

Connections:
GND: C1.2, J1.7, J2.2, J3.5
INT1_8700: J1.3, J3.1
INT1_21002: J1.5, J3.8
INT2_8700: J1.4, J3.3
INT2_21002: J1.6, J3.9
RST_21002: C1.1, J1.8, J2.1, J2.3, J2.7, J2.9, J3.7, R1.1, R2.1
SCL: J1.1, J2.4, R2.2
SDA: J1.2, J2.5, R1.2

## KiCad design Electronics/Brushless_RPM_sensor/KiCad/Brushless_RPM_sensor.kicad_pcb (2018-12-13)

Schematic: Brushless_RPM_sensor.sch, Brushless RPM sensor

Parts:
C1: 100n; C_1206_HandSoldering
J1: PHASE A; SolderWirePad_single_1-2mmDrill
J2: PHASE B; SolderWirePad_single_1-2mmDrill
J3: JR Connector; Pin_Header_Angled_1x03_Pitch2.54mm
R1: 10k/22k; R_Axial_DIN0207_L6.3mm_D2.5mm_P10.16mm_Horizontal
R2, R3, R4: 470; R_1206_HandSoldering
R5: 220; R_1206_HandSoldering
R6, R7, R9: 1k; R_1206_HandSoldering
R8: 10k; R_1206_HandSoldering
U1, U2: PC817; DIP-4_W7.62mm
U3: MCP6002-xP; DIP-8_W7.62mm

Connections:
+5V: J3.3, R2.1, R6.1, U1.4, U3.8 (V+)
GND: C1.2, J3.2, R3.2, R7.2, U2.3, U3.4 (V-)
unnamed: C1.1, R4.1, U3.3 (+)
unnamed: J1.1, R1.1
unnamed: J2.1, U1.2, U2.1
unnamed: R1.2, U1.1, U2.2
unnamed: R2.2, R3.1, R4.2, U1.3, U2.4
unnamed: R5.1, U3.1, U3.2 (-)
unnamed: R5.2, R8.2, U3.5 (+)
unnamed: R6.2, R7.1, U3.6 (-)
unnamed: R8.1, R9.1, U3.7
RPM: J3.1, R9.2

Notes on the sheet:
R1 = 10k …2s-6s R1 = 22k …7s-14s

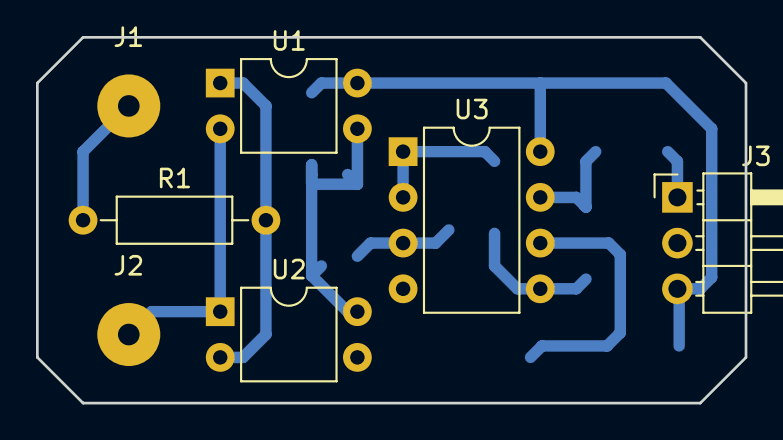
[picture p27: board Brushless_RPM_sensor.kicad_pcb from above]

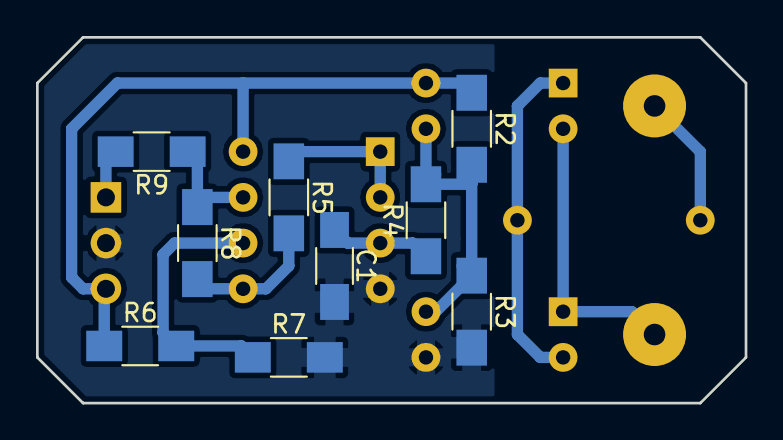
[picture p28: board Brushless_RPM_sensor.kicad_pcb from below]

Board: 2 copper layers, 39.4 x 20.3 mm, 16 parts (9 on the bottom side), 12 nets.

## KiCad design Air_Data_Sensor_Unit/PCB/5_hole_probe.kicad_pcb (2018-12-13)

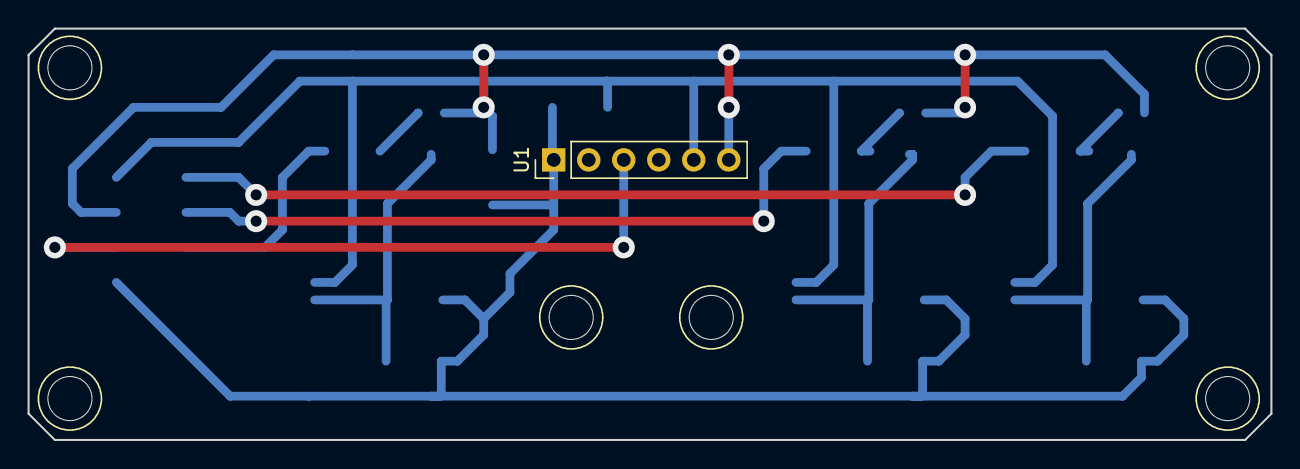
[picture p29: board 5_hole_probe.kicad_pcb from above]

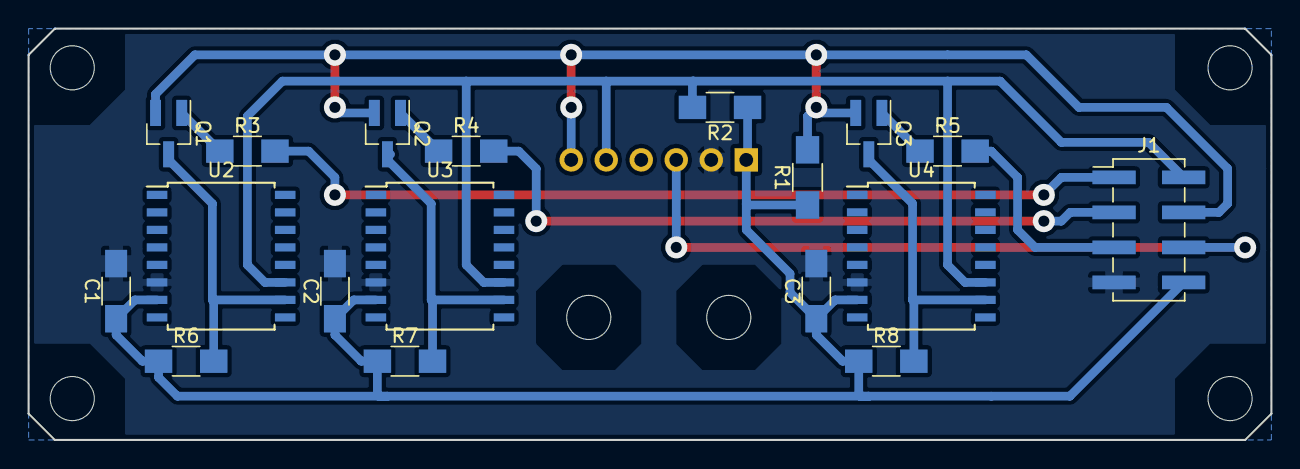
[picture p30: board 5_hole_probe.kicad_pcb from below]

Board: 2 copper layers, 90.2 x 29.8 mm, 19 parts (18 on the bottom side), 14 nets.

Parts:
C1, C2, C3: 100n; C_1206_HandSoldering
J1: ARM_HAWK_CONN; Pin_Header_Straight_2x04_Pitch2.54mm_SMD
Q1, Q2, Q3: MMBT2222; SOT-23_Handsoldering
R1, R2, R6, R7, R8: 10k; R_1206_HandSoldering
R3, R4, R5: 1k; R_1206_HandSoldering
U1: BMP085_Breakout; Pin_Header_Straight_1x06_Pitch2.54mm
U2: SM9541-020C-D-C-3-S; SOIC-16W_7.5x10.3mm_Pitch1.27mm
U3, U4: SM9541-010C-D-C-3-S; SOIC-16W_7.5x10.3mm_Pitch1.27mm

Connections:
+3V3: C1.1, C2.1, C3.1, J1.8, R1.1, R2.1, R6.1, R7.1, R8.1, U1.1, U2.7, U3.7, U4.7
EN1: J1.1, R3.2
EN2: J1.3, R4.2
EN3: J1.5, R5.2
EOC: J1.6, U1.3
GND: C1.2, C2.2, C3.2, J1.7, U1.2, U2.6, U3.6, U4.6
unnamed: Q1.1, R3.1
unnamed: Q2.1, R4.1
unnamed: Q3.1, R5.1
SCL: J1.2, R2.2, U1.5, U2.11, U3.11, U4.11
SDA: J1.4, Q1.2, Q2.2, Q3.2, R1.2, U1.6
SDA1: Q1.3, R6.2, U2.10
SDA2: Q2.3, R7.2, U3.10
SDA3: Q3.3, R8.2, U4.10

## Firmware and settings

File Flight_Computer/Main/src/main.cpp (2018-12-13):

/**
  ******************************************************************************
  * @file    main.cpp
  * @author  Daniel Pusztai
  * @version V1.0
  * @date    07-20-2016
  * @brief   Main function of ARM-Hawk.
  ******************************************************************************
*/

// Built in modules
#include "stm32f7xx.h"

// Own modules
#include "System.hpp"
#include "Datalog.hpp"

// !!! INCLUDE ALL OWN PERIPHERAL MODULES VIA 'ArmHawk.hpp' !!!
#include "ArmHawk.hpp"

// !!! DO NOT DO ANYTHING BEFOR INITIALISING 'System' OBJECT !!!
volatile MessageBuffer debug_messageBuffer;
volatile MessageBuffer datalog_messageBuffer;
System sys;

// Vehicle CG position from vehicle reference point [m]
const Vector<3> r_CG_REF({-0.017, 0.000, 0.012});

// Init all peripheral systems
AirDataComputer adc(101325, r_CG_REF);

InertialNavigationSystem ins(r_CG_REF);

Servo aileron(1, 1907, 1525, 1062);
Servo elevator(2, 1911, 1517, 1147);
Servo throttle(3, 1100, 1520, 1940);
Servo rudder(4, 1131, 1518, 2005);
Servo flaps(5, 1764, 1520, 1151);
Servo ch6(6);

Receiver receiver;

Propulsion propulsion(4000);

StabilityAugmentationSystem sas;

Datalog datalog;

int main(void)
{
	// Check if the user button is pressed and go into datalog readout mode if so
	if(sys.userButton_pressed())
	{
		// Read log and send to COM port
		datalog.read();

		// Erase log and wait until finished
		datalog.erase();

		// Enter an infinite loop when finished -> Restart required
		while(true);
	}

#ifdef DEBUG
	print("Debug configuration flashed", MESSAGE_NOTE);
#endif

	// Give all external systems some time to initialize
	waitMs(1000);

	// Last step of initialization
	sys.finish_initialization();
	// !!! DO NOT DO ANYTHING BELOW HERE UNTIL MAINLOOP !!!

	while(true)
	{
		// Update receiver with latest S.BUS data and switch modes according to TX CH 8
		receiver.update();

		if(receiver.failsafe || (receiver.channel[7] < -0.25f))
		{
			// Switch to Standby Mode
			if(sys.autopilot_mode != AUTOPILOT_MODE_STANDBY)
				print("Engaged Autopilot Standby Mode", MESSAGE_NOTE);

			sys.autopilot_mode = AUTOPILOT_MODE_STANDBY;
		}
		else if(sys.masterWarning || (receiver.channel[7] < 0.25f))
		{
			// Switch to Direct Mode
			if(sys.autopilot_mode != AUTOPILOT_MODE_DIRECT)
				print("Engaged Autopilot Direct Mode", MESSAGE_NOTE);

			sys.autopilot_mode = AUTOPILOT_MODE_DIRECT;
		}
		else
		{
			// Switch to Stability Mode
			if(sys.autopilot_mode != AUTOPILOT_MODE_STABILITY)
				print("Engaged Autopilot Stability Mode", MESSAGE_NOTE);

			sys.autopilot_mode = AUTOPILOT_MODE_STABILITY;
		}

		// Update the propulsion state according to the system mode
		if(sys.autopilot_mode == AUTOPILOT_MODE_STANDBY)
			propulsion.update(receiver.channel[2]);
		else
			propulsion.update(throttle.position);

		// Update Air Data Computer with last cycle INS data (1 sample lag)
		adc.update(ins.omega_V_V.filtered);

		// Update Inertial Navigation System (GPS + GYRO + ACC + MAG) with ADC altitude data and motor current
		ins.update( propulsion.I, adc.altitude, adc.v_rel);

		// Update the stability augmentation system mode and controller gains
		sas.update(adc.alpha.filtered, adc.V_T.filtered, ins.Phi, ins.n.filtered(2), propulsion.omega_P.filtered, receiver.channel[4], sys.autopilot_mode);

		// Handle autopilot
		if(sys.autopilot_mode == AUTOPILOT_MODE_STABILITY)
		{
			if((sas.ground_lock) && (receiver.channel[12] > 0.25f) && (receiver.channel[2] < -0.95f))
			{
				// Perform self-test (activated via TX channel 13, only if throttle down)
				aileron.update(sas.self_test_roll(receiver.channel[8]));
				elevator.update(receiver.channel[1]);
				throttle.update(receiver.channel[2]);
				rudder.update(sas.self_test_yaw(receiver.channel[11]));
			}
			else
			{
				// Apply feedback control to flight controls from channel inputs 9~12
				aileron.update(sas.stabilize_roll(ins.Phi(0), ins.omega_V_V.filtered(0), receiver.channel[8]));
				elevator.update(sas.stabilize_pitch(ins.Phi(1), ins.omega_V_V.filtered(1), adc.alpha.filtered, adc.V_T.filtered, 0.7f * receiver.channel[9]));
				throttle.update(sas.stabilize_speed(receiver.channel[10]));
				rudder.update(sas.stabilize_yaw(adc.beta.filtered, ins.omega_V_V.filtered(2), receiver.channel[11]));
			}
		}
		else if(sys.autopilot_mode == AUTOPILOT_MODE_DIRECT)
		{
			// Update flight controls directly from channel inputs 1~4 (inc. trim/travel modifications)
			aileron.update(receiver.channel[0]);
			elevator.update(receiver.channel[1]);
			throttle.update(receiver.channel[2]);
			rudder.update(receiver.channel[3]);
		}
		else
		{
			// Standby mode => idle flight controls (disconnected via external channel multiplexer)
			aileron.update(0.0);
			elevator.update(0.0);
			throttle.update(-1.0);
			rudder.update(0.0);
		}

		// Update the onboard log => store the latest variables and messages in the external flash
		if(sys.userButton_pressed() && (!datalog.running))
		{
			print("Datalog manual start by user button", MESSAGE_NOTE);
			datalog.start();
		}
		else if((adc.V_T.filtered > 15.0) && (!datalog.running))
		{
			print("Datalog autostart due to airspeed > 15m/s", MESSAGE_NOTE);
			datalog.start();
		}

		datalog.update();

		// Visualize Master-Warnings and Master-Cautions
		if(sys.masterWarning)
		{
			sys.LedRed_set();
		}
		else if(sys.masterCaution)
		{
			if(!(sys.tick % 50))
				sys.LedRed_toggle();
		}
		else
		{
			sys.LedRed_clear();
		}

		// Visualize the state of the Inertial Navigation System
		if((ins.state == INS_CALIBRATING) || (ins.state == INS_WAIT_FOR_GPS) || (ins.state == INS_INITIALIZING))
		{
			if(!(sys.tick % 50))
				sys.LedBlue_toggle();
		}
		else
		{
			if(!(sys.tick % 2))
				sys.LedBlue_toggle();
		}

		// Finish the mainloop => handle remaining time in 50Hz-Mainloop, if there is any
		sys.finish_mainloop();
	}
}

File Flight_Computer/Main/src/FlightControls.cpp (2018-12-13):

/*
 * FlightControls.cpp
 *
 *  Created on: May 24, 2018
 *      Author: Daniel
 */

#include "FlightControls.hpp"

char Servo::initialized = 0;

/*
 * Initialize hardware including timers to output PWM signals,
 * if not already done so.
 * @param channel		One of 6 channels to output the signals
 * @param lower_limit	Travel point for -100% input
 * @param offset		Mid-point of servo travel
 * @param upper_limit	Travel point for +100% input
 */
NO_OPTIMIZATION Servo::Servo(char channel, float lower_limit, float offset, float upper_limit)
{
	this->channel = channel;

	this->lower_limit = lower_limit;
	this->offset = offset;
	this->upper_limit = upper_limit;

	this->position = 0;

	// Check if hardware is already initialized
	if(!this->initialized)
	{
		// Init GPIOA PA0, PA1, PA2 & PA3 as very high speed, alternate function 2 for Timer5
		RCC->AHB1ENR |= RCC_AHB1ENR_GPIOAEN;
		GPIOA->MODER |= GPIO_MODER_MODER0_1 | GPIO_MODER_MODER1_1 | GPIO_MODER_MODER2_1 | GPIO_MODER_MODER3_1;
		GPIOA->OSPEEDR |= GPIO_OSPEEDER_OSPEEDR0 | GPIO_OSPEEDER_OSPEEDR1 | GPIO_OSPEEDER_OSPEEDR2 | GPIO_OSPEEDER_OSPEEDR3;
		GPIOA->AFR[0] |= (2 << 0) | (2 << 1*4) | (2 << 2*4) | (2 << 3*4);

		// Init GPIOE PE5 & PE6 as very high speed, alternate function 3 for Timer9
		RCC->AHB1ENR |= RCC_AHB1ENR_GPIOEEN;
		GPIOE->MODER |= GPIO_MODER_MODER5_1 | GPIO_MODER_MODER6_1;
		GPIOE->OSPEEDR |= GPIO_OSPEEDER_OSPEEDR5 | GPIO_OSPEEDER_OSPEEDR6;
		GPIOE->AFR[0] |= (3 << 5*4) | (3 << 6*4);

		// Init Timer5 CH1, CH2, CH3 & CH4 for high precision servo PWM output
		RCC->APB1ENR |= RCC_APB1ENR_TIM5EN;			// Enable peripheral clock
		TIM5->PSC = 0;								// Prescaler = 1 => Frequency = 108MHz
		TIM5->ARR = 2160000 - 1;					// Frequency = 50Hz
		TIM5->CCMR1 = TIM_CCMR1_OC1M_2 | TIM_CCMR1_OC1M_1 | TIM_CCMR1_OC1PE |
						TIM_CCMR1_OC2M_2 | TIM_CCMR1_OC2M_1 | TIM_CCMR1_OC2PE;
		TIM5->CCMR2 = TIM_CCMR2_OC3M_2 | TIM_CCMR2_OC3M_1 | TIM_CCMR2_OC3PE |
						TIM_CCMR2_OC4M_2 | TIM_CCMR2_OC4M_1 | TIM_CCMR2_OC4PE;		// Enable PWM mode 1 and buffering of CCR
		TIM5->CCER = TIM_CCER_CC1E | TIM_CCER_CC2E | TIM_CCER_CC3E | TIM_CCER_CC4E;	// Enable capture compare outputs
		TIM5->CCR1 = 0;
		TIM5->CCR2 = 0;
		TIM5->CCR3 = 0;
		TIM5->CCR4 = 0;								// Set all PWMs to zero (idle all servos)
		TIM5->EGR |= TIM_EGR_UG;					// Update all registers by issuing an update event
		TIM5->CR1 = TIM_CR1_ARPE | TIM_CR1_CEN;		// Buffer auto reload register, Enable Timer

		// Init Timer9 CH1 & CH2 for standard precision servo PWM output
		RCC->APB2ENR |= RCC_APB2ENR_TIM9EN;			// Enable peripheral clock
		TIM9->PSC = 71;								// Prescaler = 72 => Frequency = 3MHz
		TIM9->ARR = 60000 - 1;						// Frequency = 50Hz
		TIM9->CCMR1 = TIM_CCMR1_OC1M_2 | TIM_CCMR1_OC1M_1 | TIM_CCMR1_OC1PE |
						TIM_CCMR1_OC2M_2 | TIM_CCMR1_OC2M_1 | TIM_CCMR1_OC2PE;		// Enable PWM mode 1 and buffering of CCR
		TIM9->CCER = TIM_CCER_CC1E | TIM_CCER_CC2E;	// Enable capture compare outputs
		TIM9->CCR1 = 0;
		TIM9->CCR2 = 0;								// Set all PWMs to zero (idle all servos)
		TIM9->EGR |= TIM_EGR_UG;					// Update all registers by issuing an update event
		TIM9->CR1 = TIM_CR1_ARPE | TIM_CR1_CEN;		// Buffer auto reload register, Enable Timer

		this->initialized = 1;
	}

	// Set the servo to 0
	this->update(0.0f);
}

/*
 * Adjusts the PWM signal to drive the servo to a new position
 * @param position	Normalized position value ranging from -1.0 to 1.0
 */
void NO_OPTIMIZATION Servo::update(float position)
{
	// Check travel limit
	if(position < -1.0f)
	{
		print("Servo reached lower travel limit; Channel: ", this->channel, MESSAGE_WARNING);
		return;
	}
	else if(position > 1.0f)
	{
		print("Servo reached upper travel limit; Channel: ", this->channel, MESSAGE_WARNING);
		return;
	}

#ifndef FC_DISABLED
	this->position = position;

	// Convert normalized position input to general value in microseconds
	float position_us = 0;

	if(this->position < 0.0f)
		position_us = this->offset + this->position * (this->offset - this->lower_limit);
	else
		position_us = this->offset + this->position * (this->upper_limit - this->offset);

	// Convert microseconds to timer value and write right register according to channel
	if(this->channel == 1)
		TIM5->CCR1 = (int)roundf(position_us * 108.0f) - 1;
	else if(this->channel == 2)
		TIM5->CCR2 = (int)roundf(position_us * 108.0f) - 1;
	else if(this->channel == 3)
		TIM5->CCR3 = (int)roundf(position_us * 108.0f) - 1;
	else if(this->channel == 4)
		TIM5->CCR4 = (int)roundf(position_us * 108.0f) - 1;
	else if(this->channel == 5)
		TIM9->CCR1 = (int)roundf(position_us * 3.0f) - 1;
	else if(this->channel == 6)
		TIM9->CCR2 = (int)roundf(position_us * 3.0f) - 1;
#endif
}

// Initialization of static members of Receiver class
volatile uint8_t Receiver::sbus_buffer[25];
volatile int Receiver::sbus_pos = 0;
volatile int Receiver::usart_errors = 0;
volatile int Receiver::sbus_errors = 0;
volatile int Receiver::idle_time = 0;
volatile uint8_t Receiver::sbus_frame[25];

/*
 * Initialize all hardware necessary for reading the S.BUS input of the RC receiver
 */
NO_OPTIMIZATION Receiver::Receiver()
{
	this->frames_lost = 0;
	this->failsafe = 0;

	// Pause USART6 interrupt
	NVIC_DisableIRQ(USART6_IRQn);

	// Init GPIOC PC7 as very high speed, alternate function 8 for USART6
	RCC->AHB1ENR |= RCC_AHB1ENR_GPIOCEN;
	GPIOC->MODER |= GPIO_MODER_MODER7_1;
	GPIOC->OSPEEDR |= GPIO_OSPEEDER_OSPEEDR7;
	GPIOC->AFR[0] |= (8 << (7 * 4));

	// Init USART6 RX for S.BUS receiption
	RCC->APB2ENR |= RCC_APB2ENR_USART6EN;				// Enable peripheral clock
	RCC->DCKCFGR2 |= RCC_DCKCFGR2_USART6SEL_0;			// Set system clock as source
	USART6->CR1 = USART_CR1_M_0 | USART_CR1_PCE | USART_CR1_PEIE | USART_CR1_RXNEIE | USART_CR1_RE;		// Format 8E2, parity error & RX interrupt, enable RX
	USART6->CR2 = USART_CR2_RXINV | USART_CR2_STOP_1;	// Invert RX pin, 2 Stop bits
	USART6->CR3 = USART_CR3_EIE;						// Enable error interrupt
	USART6->BRR = 2160;									// Baud = 100000
	USART6->CR1 |= USART_CR1_UE;						// Enable USART6

	// Init Timer13 for S.BUS frame idle detection
	RCC->APB1ENR |= RCC_APB1ENR_TIM13EN;		// Enable peripheral clock
	TIM13->PSC = 9;								// Prescaler = 10 => Frequency = 10.8MHz
	TIM13->ARR = 53999;							// Frequency = 200Hz
	TIM13->DIER = TIM_DIER_UIE;					// Enable update (overflow) interrupt
	TIM13->CR1 = TIM_CR1_CEN;					// Enable timer

#ifndef FC_DISABLED
	// Enable interrupts
	NVIC_EnableIRQ(USART6_IRQn);
	NVIC_EnableIRQ(TIM8_UP_TIM13_IRQn);
#else
	// Set Master Caution if hardware is temporarly disabled for debugging
	print("Flight controls disabled for debugging", MESSAGE_CAUTION);
#endif
}
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

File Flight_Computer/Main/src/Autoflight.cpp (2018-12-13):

/*
 * Autoflight.cpp
 *
 *  Created on: Sep 30, 2018
 *      Author: Daniel
 */

#include "Autoflight.hpp"

// SAS constant members for computing interpolated linear systems (stall protetction)
const Matrix<3, 3> StabilityAugmentationSystem::p_A[10] =
{
	Matrix<3, 3>({-1.09188e-02, 1.01357e+00, -3.30995e-04, -1.15491e-02, -2.07507e-01, -1.56805e-03, 6.70906e-02, 2.70226e+00, 9.22640e-02}),
	Matrix<3, 3>({2.67871e-04, 1.63924e+01, -2.90651e-04, -2.59557e-02, -1.74242e-01, -3.67459e-03, 5.77674e-02, -4.02373e+01, -6.44761e-01}),
	Matrix<3, 3>({2.28586e-06, 2.93235e-05, -1.48847e-08, -1.28894e-07, -2.49366e-06, -3.30025e-08, -4.88796e-06, -1.05521e-04, -7.86279e-06}),
	Matrix<3, 3>({-8.68001e-05, 9.33953e-01, 1.70135e-05, -5.01559e-03, 5.82092e-03, -5.09263e-04, 1.78385e-02, 1.97568e+00, -4.87891e-02}),
	Matrix<3, 3>({-2.41515e-04, 4.07470e-03, 1.55745e-06, 1.50427e-05, 1.07690e-03, 1.04167e-05, 4.03943e-04, 2.72878e-03, 1.06207e-03}),
	Matrix<3, 3>({4.01532e-07, 6.25728e-05, 3.21849e-07, 8.83089e-08, -4.62449e-07, 2.92852e-07, 1.66376e-05, 5.86777e-04, 4.82652e-05}),
	Matrix<3, 3>({6.48708e-02, -1.48970e+01, 3.41531e-03, 5.51522e-02, 1.45164e+00, 5.45720e-03, -6.77052e-01, -1.39745e+01, -1.35364e+00}),
	Matrix<3, 3>({-3.09873e-05, -4.93062e+00, -1.54273e-04, 1.60027e-02, 1.48757e-02, 1.65574e-03, -6.04553e-02, 1.61599e+00, 1.96935e-01}),
	Matrix<3, 3>({-2.59307e-03, -1.92930e-02, 9.57609e-06, 1.12404e-04, -7.76055e-04, -6.44436e-06, 4.32162e-03, 5.29851e-02, 2.04468e-03}),
	Matrix<3, 3>({9.34336e-02, 1.11363e+01, -4.02569e-03, -1.26476e-01, -1.10589e-01, 9.73271e-01, -9.74468e-01, -1.77389e+01, -1.98304e+00})
};

const Vector<2> StabilityAugmentationSystem::p_a[10] =
{
	Vector<2>({9.22571e-02, -3.13062e-03}),
	Vector<2>({2.62018e-01, -8.63690e-03}),
	Vector<2>({-3.53314e-20, -2.37801e-21}),
	Vector<2>({-9.23924e-03, 1.52387e-01}),
	Vector<2>({-1.02484e-17, 6.21159e-19}),
	Vector<2>({-2.99065e-20, -4.96554e-20}),
	Vector<2>({-6.72585e-01, -4.36335e-03}),
	Vector<2>({-5.85732e-02, -5.33280e-01}),
	Vector<2>({5.66972e-17, 1.24957e-18}),
	Vector<2>({1.49863e+00, 9.33028e-02})
};

const float StabilityAugmentationSystem::p_B[10] =
{
	-1.91436e-01, -1.61356e+00, -1.60514e-04, 5.81003e-02, 2.04716e-02, 1.33385e-04, -2.75457e+01, 5.91662e-02, 6.66667e-02, -6.19512e+00
};

const Vector<3> StabilityAugmentationSystem::p_dx[10] =
{
	Vector<3>({3.39153e-01, -5.55424e-02, 7.45110e-01}),
	Vector<3>({-1.91918e-01, -6.83856e-01, 2.87540e+00}),
	Vector<3>({3.98514e-05, -1.11989e-06, -3.04412e-05}),
	Vector<3>({-1.28110e-02, -9.74509e-02, 3.84956e-01}),
	Vector<3>({-5.39993e-03, 2.15474e-04, 3.53171e-04}),
	Vector<3>({-4.73109e-07, -3.06472e-06, -5.54827e-04}),
	Vector<3>({-3.56669e+00, 1.87310e-01, -1.06186e+01}),
	Vector<3>({-8.87041e+00, 3.83573e-01, -1.10663e+00}),
	Vector<3>({-1.61267e-02, 2.43762e-04, 2.11693e-02}),
	Vector<3>({4.44844e+00, -1.30645e-01, 2.58801e-01})
};

/*
 * Initialize all controller gains with minimum airspeed values
 */
StabilityAugmentationSystem::StabilityAugmentationSystem()
	: G_phi_deltaA({1.0, -2.4719, 1.9969, -5.2493e-1}, {0, -1.3146e-3, -2.6292e-3, -1.3146e-3}),
	  G_beta_deltaR({1.0, -2.5589, 2.1458, -5.8323e-1}, {0, 1.3736e-3, 1.1265e-3, -2.4707e-4}),
	  G_P_deltaA({1.0, -1.4724, 5.2515e-1}, {0, -1.3119e-1, -1.3119e-1}),
	  G_R_deltaR({1.0, -2.5589, 2.1458, -5.8323e-1}, {0, -5.4292e-2, -6.7240e-5, 5.4225e-2}),
	  H_R({1.0f, -0.9855072f}, {100.0f, -100.0f}),
	  H_beta({1.0f}, {1.105f, -0.895f}),
	  A(1), a(1), B(1), dx(0)
{
	// Enable self-test and disable throttle controller until airborn for first time
	this->ground_lock = 1;

	// Roll damper
	this->k_P = -0.34f;

	// Bank controller
	this->k_phi = -2.465f;

	this->P_max = 2.3f;

	this->bank_bypass = 0;
	this->phi_cmd = 0;

	// Yaw damper
	this->k_R = -0.314f;
	this->T_R = 1.37f;

	// Turn coordinator
	this->k_beta = 0.2335f;
	this->T_beta = 10.5f;
	this->delta_R_beta = 0;

	this->beta_max = 8.0f * PI / 180.0f;
	this->beta_cmd = 0;

	// Elevator trim
	this->elevator_trim = 0;

	// Stall protection
	this->gamma = 0;
	this->stall_mode = 0;
	this->throttle_freeze = 0;
}

/*
 * Update the controller coefficients (gain scheduling) according to airspeed;
 * Idle controllers when system in manual modes
 * !!! Must be called in every mainloop iteration !!!
 * @param V_T				Airspeed from ADC [m/s]
 * @param Phi				Attitude vector (euler angles) [rad]
 * @param autopilot_mode	Current operational mode
 */
void StabilityAugmentationSystem::update(float alpha, float V_T, Vector<3> Phi, float n_z, float omega_P, float delta_F, char autopilot_mode)
{
	// Disable self test and release throttle controller once airborne
	if(V_T > 10.0f)
		this->ground_lock = 0;

	// Reset self-tests when not needed
	if(autopilot_mode != AUTOPILOT_MODE_STABILITY)
	{
		this->G_phi_deltaA.reset();
		this->G_beta_deltaR.reset();
		this->G_P_deltaA.reset();
		this->G_R_deltaR.reset();
	}

	// Limit airspeed to avoid unreasonable gains
	if(V_T < 15.0f)
		V_T = 15.0f;
	else if(V_T > 40.0f)
		V_T = 40.0f;

	// Roll damper
	this->k_P = -0.58f + 0.016f * V_T;
	if(this->k_P > 0.0f)
		this->k_P = 0.0f;

	// Bank controller
	this->k_phi = -3.23f + 0.051f * V_T;
	if(this->k_phi > 0.0f)
		this->k_phi = 0.0f;

	this->P_max = 0.425f + 0.125f * V_T;
	if(this->P_max < 0.0f)
		this->P_max = 0.0f;

	this->bank_bypass = (autopilot_mode != AUTOPILOT_MODE_STABILITY) || (abs(Phi(1)) > (PI / 3.0f));

	if(this->bank_bypass)
		this->phi_cmd = Phi(0);

	// Yaw damper
	this->k_R =  -0.44f + 0.0084f * V_T;
	if(this->k_R > 0.0f)
		this->k_R = 0.0f;

	this->T_R = 0.56f + 0.054f * V_T;
	this->H_R.a[1] = (1.0f / this->T_R - 100.0f) / (1.0f / this->T_R + 100.0f);

	if(autopilot_mode != AUTOPILOT_MODE_STABILITY)
		this->H_R.reset();

	// Turn coordinator
	this->k_beta = 0.37f - 0.0091f * V_T;
	if(this->k_beta < 0.0f)
		this->k_beta = 0.0f;

	this->T_beta = -12.0f + 1.5f * V_T;
	this->H_beta.b[0] = this->T_beta / 100.0f + 1.0f;
	this->H_beta.b[1] = this->T_beta / 100.0f - 1.0f;

	if(autopilot_mode != AUTOPILOT_MODE_STABILITY)
	{
		this->H_beta.reset();
		this->delta_R_beta = 0;
		this->beta_cmd = 0;
	}

	// Compute static elevator trim
	this->elevator_trim = -0.01f * (SAS_ELEVATOR_ZERO_TRIM + (SAS_ELEVATOR_FLAP_TRIM - SAS_ELEVATOR_ZERO_TRIM) * delta_F);

	// Compute flight path angle
	this->gamma = asin(sin(Phi(1)) * cos(alpha) - cos(Phi(0)) * cos(Phi(1)) * sin(alpha));

	// Stall protection gains
	if(n_z < 1.0f)
		n_z = 1.0f;

	// TODO vvv This got added vvv
	if(this->gamma > (PI / 3.0f))
		this->gamma = PI / 3.0f;
	else if(this->gamma < (-PI / 3.0f))
		this->gamma = -PI / 3.0f;

	// TODO vvv This got changed vvv
	this->x_0(0) = 17.97f * sqrt(n_z);
	this->x_0(1) = SAS_ALPHA_PROT;
	this->x_0(2) = 10.03f * cos(Phi(1)) / this->x_0(0) * (n_z * cos(this->gamma) / 0.9781f - 0.9781f / (n_z * cos(this->gamma)));

	float y[9] = {n_z * n_z, Phi(1) * Phi(1), omega_P * omega_P, n_z * Phi(1), n_z * omega_P, Phi(1) * omega_P, n_z, Phi(1), omega_P};
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
